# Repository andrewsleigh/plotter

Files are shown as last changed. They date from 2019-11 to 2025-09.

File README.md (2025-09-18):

<p>
<div class="video-responsive">
<iframe width="800" height="450" src="https://www.youtube.com/embed/pfx2bN_xx8s" frameborder="0" allow="accelerometer; autoplay; encrypted-media; gyroscope; picture-in-picture" allowfullscreen></iframe>
</div>
</p>

* **Update: 2020-03-04. I'm currently on version 3 of the design – scroll down to see the current design and download files**
* **Update: 2021-07-06. I've added a [BOM](#bom), after many requests!**
* **Update: 2021-11-25. Added an alternative [US-centric BOM](#us-bom), shared by a fellow maker**
* 

## Support my work!

If you like this project or would like to say thanks, you can buy my plotter artwork from https://penuppendown.square.site. I'd really appreciate your support :) 

## Background

I've always enjoyed the aesthetics of pen plotters, both in the way they operate, and their output. And unlike most digital machines that interface with the physical world, they actually get better at the transition point. Laser cutters make a smell, they burn or melt edges and leave behind a kerf. 3D printers are slow, and leave behind layer lines or heaps of PLA spaghetti. But pen plotters have a delightful slow, deliberate movement that is both cleanly digital and unavoidably textured.

I have an old HP 7475A plotter, but I wanted to try making my own. Not least because I've just made a 1-axis CNC machine ([a camera slider](../fab-slider)) so wanted to continue learning by adding another axis. In particular, I learned from the previous project that getting a machine to 90% good enough is easy. The real work is in that last 10%. If I want to create really good plots, I need to make a really good plotter.

## Version 1: Endless Plotter

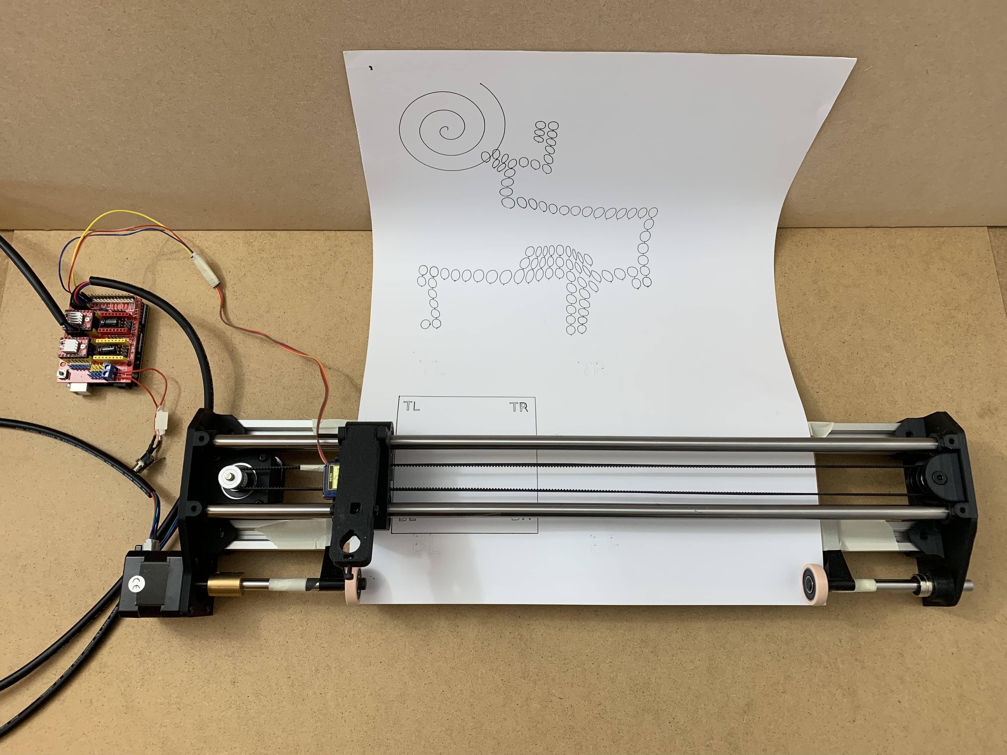
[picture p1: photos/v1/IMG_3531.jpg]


I was inspired to start this project when I saw [this plotter featured on Hackaday](https://hackaday.com/2019/08/26/3d-printed-pen-plotter-is-as-big-as-you-need-it-to-be/). As well as being nicely finished, it has a clever design that moves the pen in one axis, and the paper in the other, much like a commercial plotter or inkjet printer.

This has a couple of nice benefits: 
* It has a more compact footprint (when not in use) – it's only as big as its x-axis.
* It can, in theory, plot an endlessly large (in the y-axis) piece of artwork.

I made a version of this plotter, adapting the original 3D files and had some success  with it in practice, but I eventually decided this format was too compromised for me – I couldn't get the paper to feed back and forth reliably. So I switched to a more traditional 'Cartesian' format for version 2, where the y-axis is carried on top of the x-axis, and the plotter sits on top of the paper.

However, I've shared my 3D files here for others to use if interested. Most of the parts have been redesigned from scratch, except for the pen carriage, which is pretty close to the original design by [Ufficio Progetti Perduti](https://www.thingiverse.com/thing:3789969)

* [3D files on Thingiverse](https://www.thingiverse.com/thing:3986756)
* [3D files on Github](https://github.com/andrewsleigh/plotter/tree/master/3d-parts/v1)
* [Photos on Github](https://github.com/andrewsleigh/plotter/tree/master/photos/v1)

## Version 2: Cartesian Plotter

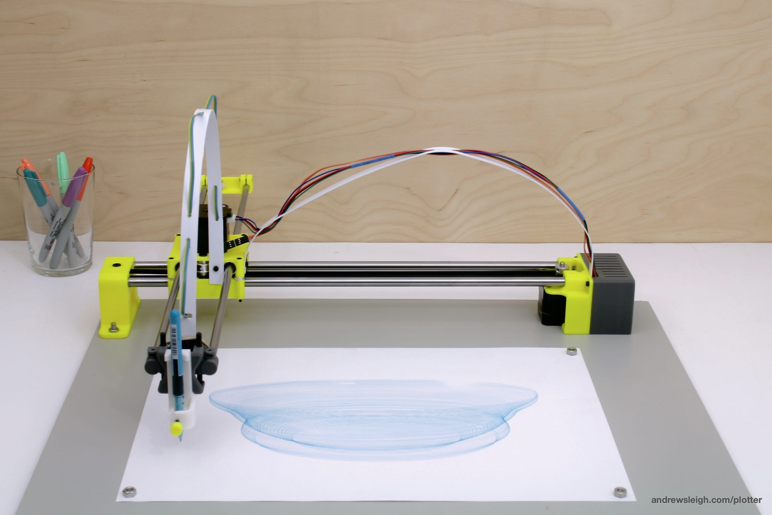
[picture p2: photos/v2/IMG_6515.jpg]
Plotter v2


This version builds on what I learned with version 1. Most obviously, it uses a traditional 'cartesian' design, where movement in the y-axis is provided by a motorized arm, while the drawing surface stays still. This has the benefit of much greater accuracy. It also means that you can, in theory, draw on any flat surface. 

However the drawbacks are that:

1. It needs much more space. With about 50 cm of travel in each axis, it needs a space that big to store, and 1 m x 50 cm to operate.
2. The long arm (with steel rods in my case) is heavy, so it tends to dip towards the end of its reach. This can cause problems getting the right pen height or pressure. To alleviate this, my design has bolt-down points on the x-axis. By bolting this axis to a piece of plywood, the frame is much stiffer. 

Some other features worth noting: 

* I'm using small sections of kite poles to hold the two parts of the pen lifter assembly together. I found 0.1 mm of extra clearance on one part was enough to allow smooth running without wobble.

* In an idea I lifted from Evil Mad Scientist's AxiDraw, I'm using thin strips of flexible polypropylene plastic to support the wires to the servo and y-axis stepper. 

### 3D design

* [3D files on Thingiverse](https://www.thingiverse.com/thing:4037180)
* [3D files on Github](https://github.com/andrewsleigh/plotter/tree/master/3d-parts/v2)
* [Photos on Github](https://github.com/andrewsleigh/plotter/tree/master/photos/v2)

### Photos and video

<p>
<div class="video-responsive">
<iframe width="800" height="450" src="https://www.youtube.com/embed/Z99n9q5OYKk" frameborder="0" allow="accelerometer; autoplay; encrypted-media; gyroscope; picture-in-picture" allowfullscreen></iframe>
</div>
</p>

There's a short demo on YouTube: <https://youtu.be/Z99n9q5OYKk>  
And lots of photos on Github: <https://github.com/andrewsleigh/plotter/tree/master/photos/v2>

## Version 3: Cartesian Plotter with V-slot axis

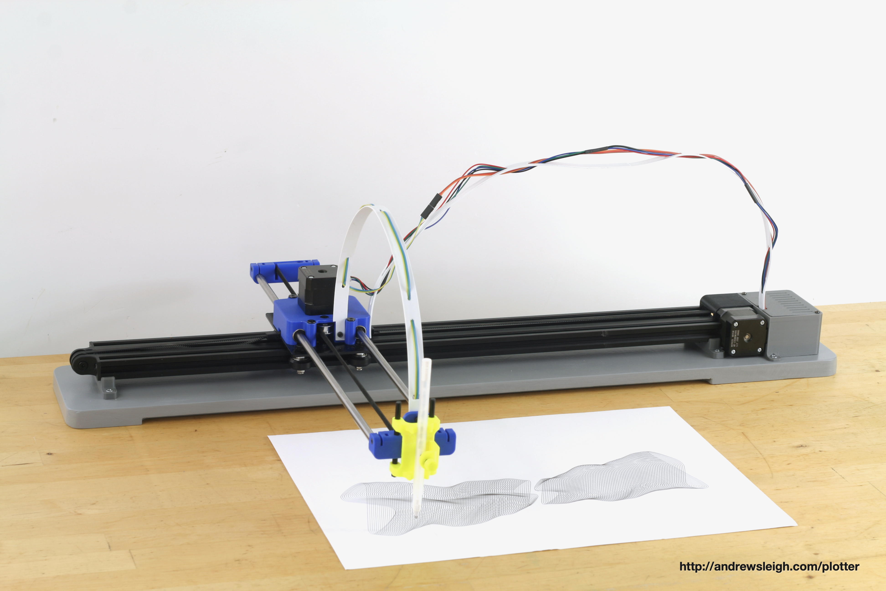
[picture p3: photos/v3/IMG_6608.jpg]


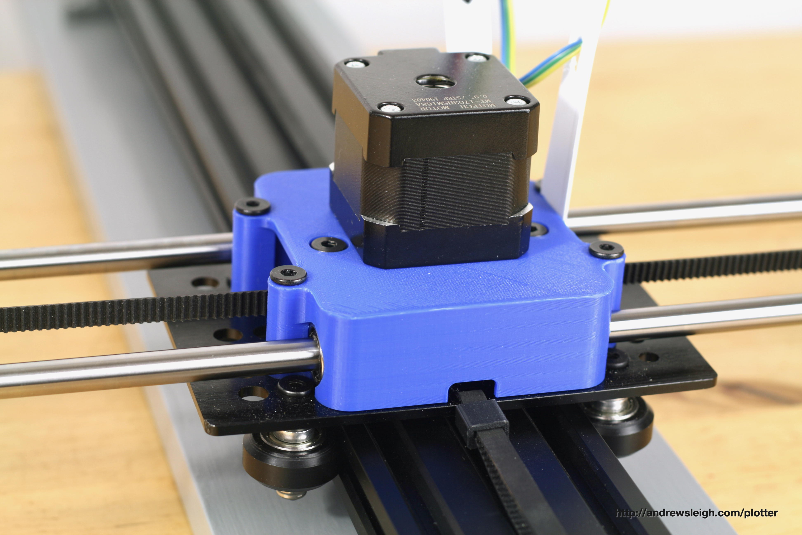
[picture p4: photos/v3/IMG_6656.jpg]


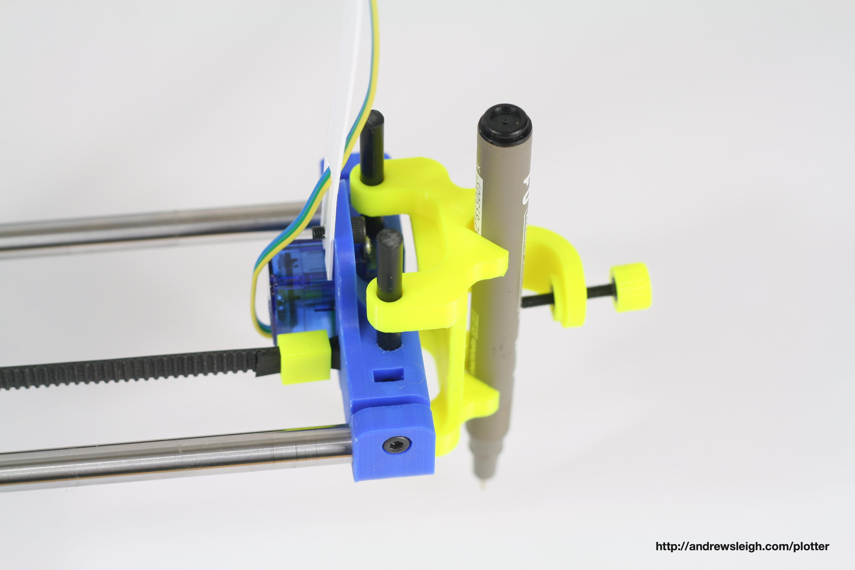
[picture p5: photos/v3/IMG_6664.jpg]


Previous designs used 10mm steel rods for the x-axis. These are prone to flexing in the assembly, and the linear bearings are also noisy. So I wanted to switch to a design that used a wheeled gantry sliding on v-slot aluminium extrusion. 

I tried a quick test by hacking a previous project and bolting my existing y-axis to a single axis slide I already had. This worked very well and convinced me it would be worth building a proper x-axis with v-slot.

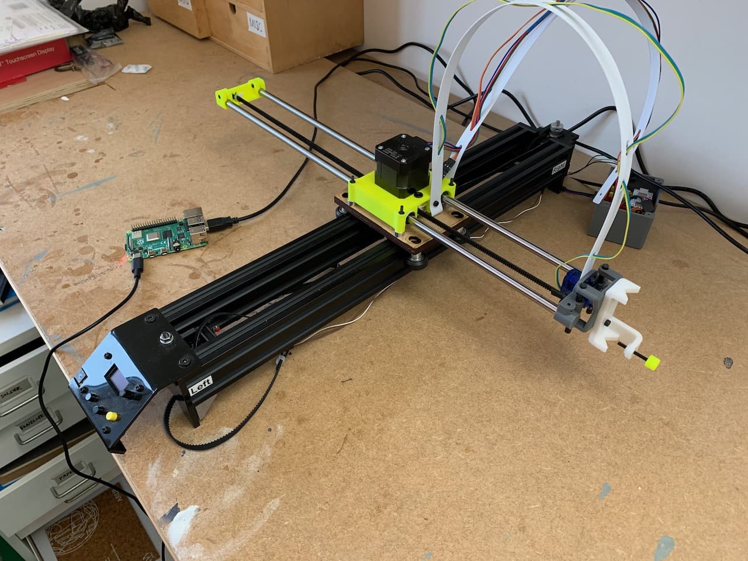
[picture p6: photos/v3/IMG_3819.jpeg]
Plotter v3 prototype


I already had 2 lengths of 2020 v-slot from my first build, so I initially used these, and made a simple assembly that gained rigidity by bolting these down to a wooden base. 

I ordered a standard v-slot gantry from China, which cost about £10-12, including wheels, bolts and spacers – including eccentric spacers. This allowed me to get a very good fit of the gantry on the x-axis for smooth quiet motion. 

If you don't want to buy an aluminum gantry, could can easily cut one on a laser (as I did for my prototype) or 3D print one from the OpenBuilds design. 

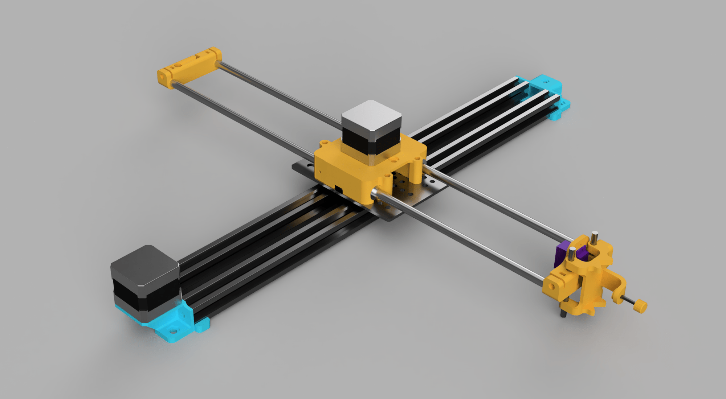
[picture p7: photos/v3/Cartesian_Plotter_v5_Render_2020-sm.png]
Plotter v3 2020


Note, you'll need to tap M5 holes into the ends of the v-slot to attach the two end brackets. The feet are bolted from underneath into the v-slot. 

But then I came into the possession(!) of a 70 cm lngth of 2060 v-slot, so I was able to make a longer, even more stable x-axis. I needed to switch the orientation of the x-axis motor, and raise the axis a little more off the ground to enable th timing belt to go over and under the 2060. I also had to fit a larger 30 tooth pulley. 

But otherwise the principle is the same, I just did a little more work to integrate the electronics and motor. 

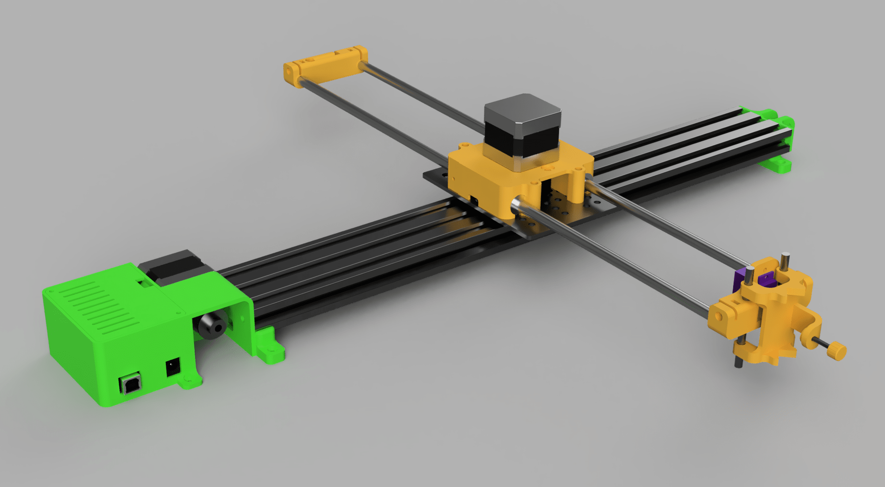
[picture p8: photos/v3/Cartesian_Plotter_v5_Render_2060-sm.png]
Plotter v3 2060


### 3D design

* [3D files on Thingiverse](https://www.thingiverse.com/thing:4200863)
* [3D files on Github](https://github.com/andrewsleigh/plotter/tree/master/3d-parts/v3)
* [3D assembly on Fusion online](https://a360.co/48olCzT)
* [Photos on Github](https://github.com/andrewsleigh/plotter/tree/master/photos/v3)

### Improvements over earlier versions

* More stable x-axis (and so less drooping of the pen at it's furthest y-extension)
* Much quieter motion on the x-axis, after swapping out linear bearings fora wheeled gantry
* X-axis can be screwed down to a solid base for greater stability
* Improved brackets for timing belt and linear rods on y-axis so belt can be more easily removed or tightened
* Simplified and more compact pen lifter
* Housing for Arduino and CNC shield can be removed or re-modelled easily (e.g. to fit a smaller Nano-based CNC shield)
* Base has a rebate to fit a 60 cm cutting mat, to allow easier alignment of paper for plotting

<a name="bom"/>

## Bill of Materials (BOM)

It’s difficult to give a comprehensive BOM because there is so much flexibility in the design, and so many choices depend on what you have to had. Nevertheless, here is an attempt at a reasonable baseline.

### Motion Control

* Arduino Uno (I’d recommend a genuine Arduino to reduce the risk of EM interference which can play havoc with your servo motor)
* Motor Control Shield
* 2 x Stepper Drivers (A4988-style, but I’d recommend Trinamic drivers for quieter operation)
* 2 x Nema 17 Stepper motors (‘17’ refers to the physical size, you will need to specify the power as well. I used these 7 oz ones from Ooznest, which are fine: https://ooznest.co.uk/product/nema17-stepper-motors/

I’m this configuration the motor control shield is mounted on the Arduino, and the stepper drivers mounted on the shield. You can also get versions that mount a smaller Arduino Nano on to the shield, alongside the drivers, which would make for a more compact design that does the same thing. You would need to adapt the Arduino housing to fit this config.

### X Axis

* Length of 2060 V-Slot aluminium extrusion.
 
(I used a 75 cm length, but anything from 40 cm up is good. Make sure you use V slot and not one of the other profiles of extrusion.An earlier version used two lengths of 2020 extrusion with a 20 mm gap in between. It doesn’t matter, just use what you have. A single piece of 2060 is stiffer, which means less drooping of the pen end and so more reliable plotting, but you could easily make other designs stiffer.)

You will need to tap M5 holes in the ends of the extrusion. 

* 2GT Timing belt (buy a length about 2.5 x the length of your extrusion. (e.g. https://ooznest.co.uk/product/2gt-gates-open-timing-belt-per-metre/)

* 30-tooth 2GT pulley (for 6 mm belt, 5 mm bore) e.g. https://ooznest.co.uk/product/2gt-pulleys/

(This pulley has a large enough diameter to run the belt on either side of the extrusion. If you want to run the belt in a gap inside some extrusion (or you’re using the 2020 design) you’ll need a smaller diameter pulley. You could print one.)

* Idler pulley (of roughly the same diameter as your main pulley) e.g. https://ooznest.co.uk/product/2gt-smooth-idler/. You could also print one.

3D printed parts:

* End bracket for idler pulley
* End bracket for motor
* Shield for motor end (purely cosmetic)
* Box and lid for Arduino
* Feet

### Gantry and Y-axis

* Large v-slot gantry kit (I got mine direct from China, or you can laser cut or 3D print your own)
* 2 x small idler pulleys for y-axis (not the larger Openbuilds pulleys)
* 4 x 8 mm (8UU) linear bearings 
* 2 x 8 mm linear rods

3D printed parts:

* Gantry case

### Pen Lifter

* SG90 Servo motor (e.g. https://thepihut.com/products/towerpro-servo-motor-sg90-hv-continuous-rotation)
* 3 wire jumper extension to extend the wires form the servo back to the motor control board
* 2 x smooth 5 mm diameter rods (I used rods from an old kite. Any smooth, consistent-diameter rods will do, but you will need to adapt the 3D files to fit)

3D printed parts:

* Y axis pen end bracket
* Y axis other end bracket
* Pen lifter
* 3mm bolt cap

### Other Hardware

* Low profile M5 bolts to attach brackets to V-Slot
* Various M3 bolts and nutes (get a selection box)
* Drop-in Tee Nuts for V-Slot e.g. https://ooznest.co.uk/product/drop-in-tee-nuts/
* Some GT2 belt clips, such as cable ties, or these nice removable clips: <http://www.thingiverse.com/thing:2354961>

(In the UK, I'd recommend Ooznest for all the materials you need to buy.)

<a name="us-bom"/>

## BOM (USA)

Fellow plotter plotter ('plotterer'?) [Kameron Keller](https://www.kameronkeller.com) kindly shared this BOM that he put together based on his build. And he's based in the US, so there are some US Amazon links in there which may be useful to some. Thanks Kameron.

| Part Number | Qty | Description | PRICE EA. | Description | Link |
| --- | --- | --- | --- | --- | --- |
| M5 - .80 | 2 | LOCKING NUT | 0.4 | FOR IDLER PULLEYS | |
| M3 X 8 | 4 | SCREW | 0.27 | WIRE GUIDE- FOR MOUNTING PLASTIC ON Y-AXIS (2)<br>(2) FOR HOLDING ARDUINO TO BOX | |
| M5 X 10 | 3 | SCREW - COUNTERSUNK | 0.35 | USED 2 FOR LARGE IDLER PULLEY 3D PRINTER PART MOUNTING TO 2060 RAIL | |
| M3 X 6 | 17  | SCREW | 0.23 | USED 12<br>X-AXIS WIRE HOLDER (2)<br>NEMA 17 MOUNTING (8)<br>ARDUINO LID (2) | |
| M3 X 12 | 4 | SCREW - PAN HEAD | 0.33 | LINEAR ROD CLAMP SCREWS (4) | |
| M3 - .5 | 14  | NUT | 0.13 | USED 12<br>LINEAR ROD CLAMP (4)<br>WIRE GUIDE (4)<br>X-AXIS WIRE HOLDER (2)<br>MOUNTING ARDUINO TO BOX (2) | |
| M3 X 30 | 1 | SCREW - SOCKET HEAD | 0.85 | PEN HOLDER | |
| M5 | 10  | WASHERS | 0.14 | USED 8 FOR IDLER PULLEY | |
| M5 X 10 | 4 | SCREW - PAN HEAD | 0.35 | 2060 VSLOT BASES | |
| M5 X 8 | 2 | SCREW - PAN HEAD | 0.2 | USED 2 FOR MOUNTING STEPPER MOTOR TO 2060 RAIL (ON END WITH ARDUINO) | |
| M5 X 35 | 4 | SCREW - PAN HEAD | 0.55 | FOR MOUNTING STEPPER MOTOR ASSEMBLY TO GANTRY PLATE, HAD TO CUT DOWN FOR CLEARANCE | |
| M5 - .80 | 8 | NUT | 0.16 | STEPPER MOTOR ASSEMBLY TO GANTRY PLATE (4) | |
| M5 X 25 | 3 | SCREW - COUNTERSUNK | 0.55 | USED 2 FOR IDLER PULLEYS | |
| SG-90 | 1 | SERVO | 2.75 | PIN LIFTER (4 PACK, $10.99) | [https://www.amazon.com/gp/product/B07MLR1498/ref=ppx\_yo\_dt\_b\_asin\_title\_o05\_s03?ie=UTF8&psc=1](https://www.amazon.com/gp/product/B07MLR1498/ref=ppx_yo_dt_b_asin_title_o05_s03?ie=UTF8&psc=1) |
| | 2 | 7 CM X 5MM CARBON RODS | 12.49 | PEN LIFTER (FOR 5 PCS, CUT DOWN TO 7 CM) | [https://www.amazon.com/gp/product/B07P81VMPF/ref=ppx\_yo\_dt\_b\_asin\_title\_o04\_s00?ie=UTF8&psc=1](https://www.amazon.com/gp/product/B07P81VMPF/ref=ppx_yo_dt_b_asin_title_o04_s00?ie=UTF8&psc=1) |
| | 2 | LINEAR RODS 8MM X 500MM | 9.95 | Y AXIS (2 PACK) | [https://www.amazon.com/gp/product/B07DPFH7HL/ref=ppx\_yo\_dt\_b\_asin\_title\_o05\_s02?ie=UTF8&psc=1](https://www.amazon.com/gp/product/B07DPFH7HL/ref=ppx_yo_dt_b_asin_title_o05_s02?ie=UTF8&psc=1) |
| | 66  | GT2 TIMING BELT ~ 66 INCHES | 11.99 | CAME WITH 196 INCHES | [https://www.amazon.com/gp/product/B0776KXY8G/ref=ppx\_yo\_dt\_b\_asin\_title\_o05\_s01?ie=UTF8&psc=1](https://www.amazon.com/gp/product/B0776KXY8G/ref=ppx_yo_dt_b_asin_title_o05_s01?ie=UTF8&psc=1) |
| | 1 | 20 TOOTH, 5MM TIMING PULLEY ^ INCLUDED WITH BELT | | CAME IN 8 PACK | |
| | 4 | LINEAR BEARINGS, 8 X 15 X 24MM | 0.84 | CAME IN 12 PACK | [https://www.amazon.com/gp/product/B08GSK5ZQB/ref=ppx\_yo\_dt\_b\_asin\_title\_o05\_s03?ie=UTF8&psc=1](https://www.amazon.com/gp/product/B08GSK5ZQB/ref=ppx_yo_dt_b_asin_title_o05_s03?ie=UTF8&psc=1) |
| | 2 | 5MM IDLER PULLEYS FOR 6MM TIMING BELT<br>INNER DIAMETER = 12 MM<br>FLANGE DIAMETER = 18 MM<br>BORE = 5MM<br>WIDTH = ~9MM | 1.6 | (CAME IN PACK OF 5) | [https://www.amazon.com/gp/product/B01H3F8LUU/ref=ppx\_od\_dt\_b\_asin\_title\_s03?ie=UTF8&psc=1](https://www.amazon.com/gp/product/B01H3F8LUU/ref=ppx_od_dt_b_asin_title_s03?ie=UTF8&psc=1) |
| | 1 | GANTRY PLATE KIT | 39.59 | | [https://www.amazon.com/gp/product/B08LDM3QFD/ref=ppx\_yo\_dt\_b\_asin\_title\_o05\_s01?ie=UTF8&psc=1](https://www.amazon.com/gp/product/B08LDM3QFD/ref=ppx_yo_dt_b_asin_title_o05_s01?ie=UTF8&psc=1) |
| | 1 | 2060 LINEAR RAIL - 500MM | 21.99 | | [https://www.amazon.com/gp/product/B08GCQXDBR/ref=ppx\_yo\_dt\_b\_asin\_title\_o05\_s00?ie=UTF8&psc=1](https://www.amazon.com/gp/product/B08GCQXDBR/ref=ppx_yo_dt_b_asin_title_o05_s00?ie=UTF8&psc=1) |
| | 2 | NEMA 17 42MM X 40MM, 0.46 NM TORQUE | 17.59 | | [https://www.amazon.com/gp/product/B06XSYP24P/ref=ppx\_yo\_dt\_b\_asin\_title\_o05\_s01?ie=UTF8&psc=1](https://www.amazon.com/gp/product/B06XSYP24P/ref=ppx_yo_dt_b_asin_title_o05_s01?ie=UTF8&psc=1) |
| | 6 | SMALL WOOD SCREWS FOR MOUNTING ENTIRE ASSEMBLY TO PIECE OF WOOD | | | |
| | 2 | SMALL SCREWS FOR MOUNTING ARDUINO LID | | | |
| | 4 | M5 T-SLOT NUTS | 0.08 | | [https://www.amazon.com/gp/product/B07NZKK1PM/ref=ppx\_yo\_dt\_b\_asin\_title\_o02\_s00?ie=UTF8&psc=1](https://www.amazon.com/gp/product/B07NZKK1PM/ref=ppx_yo_dt_b_asin_title_o02_s00?ie=UTF8&psc=1) |
| | 1 | ARDUINO UNO CNC KIT (off brand) | 17.99 | | [https://www.amazon.com/gp/product/B06XHKSVTG/ref=ppx\_yo\_dt\_b\_asin\_title\_o05\_s03?ie=UTF8&psc=1](https://www.amazon.com/gp/product/B06XHKSVTG/ref=ppx_yo_dt_b_asin_title_o05_s03?ie=UTF8&psc=1) |
| | 1 | CNC SHIELD EXPANSION BOARD | | CAME WITH ARDUINO KIT | |
| | 2 | A4988 DRIVERS | | CAME WITH ARDUINO KIT - JUMPERS INCLUDED | |
| | 1 | 30 TOOTH 5MM BORE TIMING PULLEY | 3.99 | CAME IN PACK OF 2 | [https://www.amazon.com/gp/product/B089LW6XTV/ref=ppx\_yo\_dt\_b\_asin\_title\_o05\_s03?ie=UTF8&psc=1](https://www.amazon.com/gp/product/B089LW6XTV/ref=ppx_yo_dt_b_asin_title_o05_s03?ie=UTF8&psc=1) |
| | 1 | PLASTIC FOR SALE SIGN USED FOR MAKING WIRE HOLDERS | 4.99 | | |
| | 1 | SMOOTH IDLER PULLEY KIT | 5.99 | | [https://openbuildspartstore.com/smooth-idler-pulley-kit/](https://openbuildspartstore.com/smooth-idler-pulley-kit/) |

## Electronics

I'm using an Arduino Uno with a CNC shield and two stepper drivers. I prototyped with the standard (and cheap) A4988 drivers, but switched over to Trinamic drivers which chop much more smoothly down to 1/256 microsteps, resulting in much quieter motion.

You can use pretty much any Trinamic driver board. There is a good comparison here: <https://learn.watterott.com/silentstepstick/comparison/>

## Power

The plotter requires 12V power, and your supply should be good enough to supply the current your steppers demand. (Mine is a 1.5A 12V supply)

You can plug this straight into the 12V barrel jack on the Arduino, which will give 5V reulated power to the Arduino, and 12V onto the CNC shield. 

**BUT YOU MUST HACK YOUR CNC SHIELD FIRST:** You need to wire the VIN pin on the CNC shield to the positive power terminal. Like this: http://3dpburner.blogspot.com/p/bluetooth-connection.html?m=1

### Software and Workflow

The plotter expects G-Code commands. Typically these are used by CNC machines such as mills, 3D printers and laser cutters. Most of the instructions are shared between machine types except at the business end. The plotter expects pen up and pen down commands to move the pen. (In HPGL, the language used by HP plotters, these are `PU` and `PD`.) Here, we can piggy back on G-Code commands intended to control the power of a laser. So where a laser cutter might start a line by switching the laser on to a certain power, we can use the same command but send it to the servo to move the wiper and drop the pen. This is what the modified Grbl firmware does. 

The chain of tools/processes is basically:

Create artwork > export as vectors (SVG, PDF, etc) > Create GCODE from vector file > Stream GCODE to Arduino > Use Grbl firmware on Arduino to control motors

### Art

Most of my plots are procedurally generated in Processing or p5. I write sketches that are optimised to create continuous lines and curves: no pixel data or, colours or line styles. So far, I haven't figured out a way to use the 3D renderer in p5, and still be able to export the artwork as an SVG. Either way, I start with vector line art.

I also use Blender, which has loads of options for exporting 2D vector data from 3D models.

### Create GCODE

After too much time wasted with Inkscape plug-ins I have switched to [Lightburn](https://lightburnsoftware.com) to create GCode. I find it works well with PDF files.

### Stream GCODE

There are numerous GRBL interfaces available, and I've always had good results with [CNCJS](https://cnc.js.org), which is bundled up as a webview inside a Mac app. However, that can hog the machine CPU, and also means your laptop is tethered to the plotter. So now I [run CNCJS on a local Node server on a Raspberry Pi](https://cnc.js.org/docs/rpi-setup-guide/) (Model 4, 2GBRAM) connected by USB cable to the plotter. It auto-runs as soon as the Pi boots, and I can access it through a web browser to start a job or check in later. I can always switch to CNCJS running on the laptop by unplugging the Pi.

The plotter expects a stream of GCode commands to control the motors. There are many ways you can chain together software to get to this stage. Working backwards from the plotter:

### Motor control

The Arduino is loaded with Grbl firmware, pretty much stock, but I'm using one of the many variants that lets you control a servo for pen up and pen down.

<https://github.com/robottini/grbl-servo>

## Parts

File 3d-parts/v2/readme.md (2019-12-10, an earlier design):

# Readme

These parts are for version 2 of the plotter, which uses a cartesian design.

These are STL exports from Fusion 360. There is also a Fusion 360 archive file of the whole model.

If you'd like to remix this model, please take a look at the [Thingiverse project page](https://www.thingiverse.com/thing:4037180) and consider adding attribution there.

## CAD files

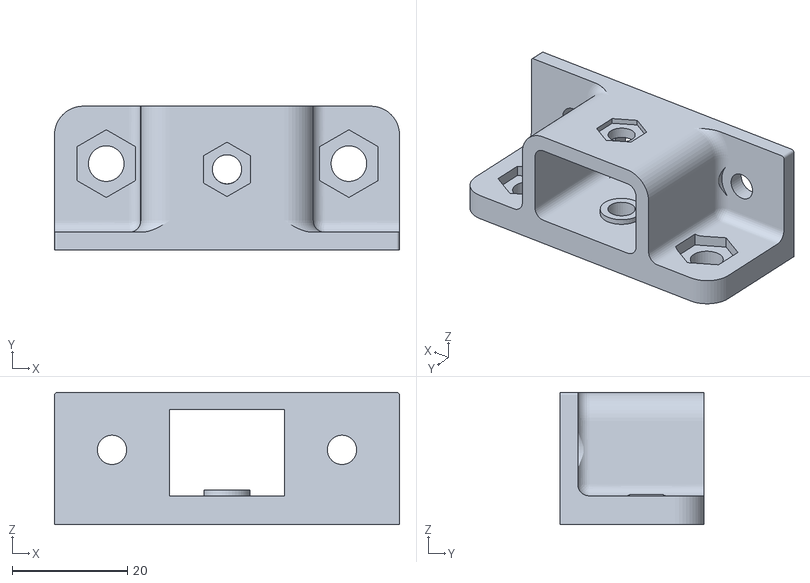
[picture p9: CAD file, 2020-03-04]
3d-parts/v3/2020_x-axis/2020_x-axis_other-end-bracket.stl
60.0 x 25.0 x 23.0

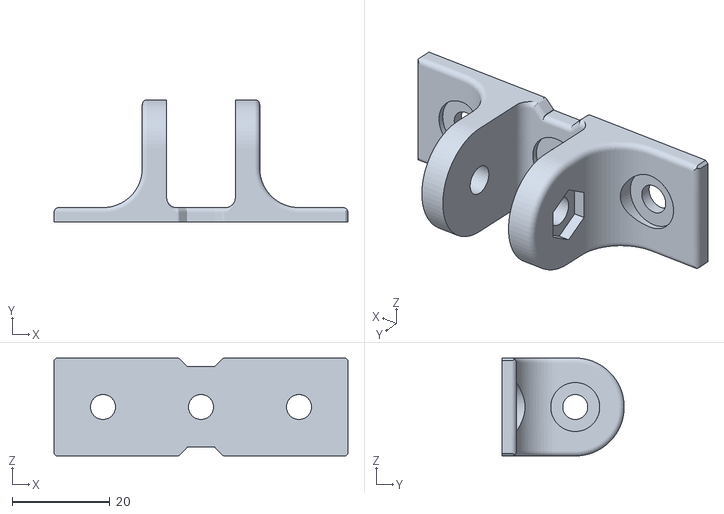
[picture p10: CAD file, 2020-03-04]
3d-parts/v3/2060_x-axis/2060_x-axis_other-end-bracket.stl
60.0 x 25.0 x 20.0

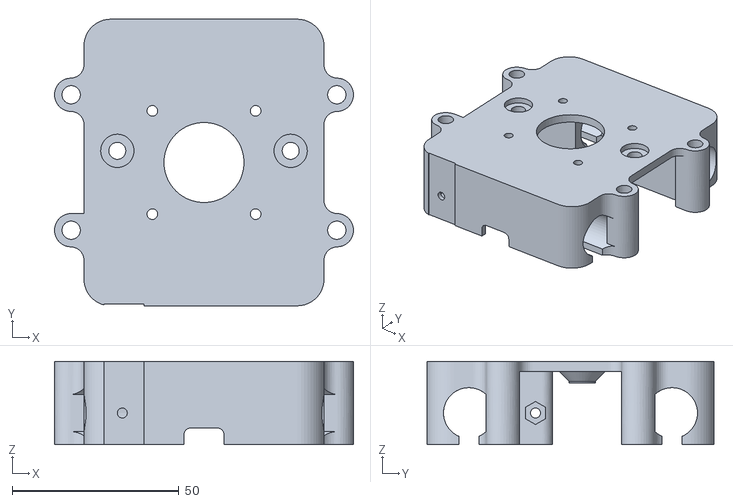
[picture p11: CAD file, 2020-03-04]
3d-parts/v3/y-axis/y-axis_gantry.stl
89.7 x 86.0 x 25.0

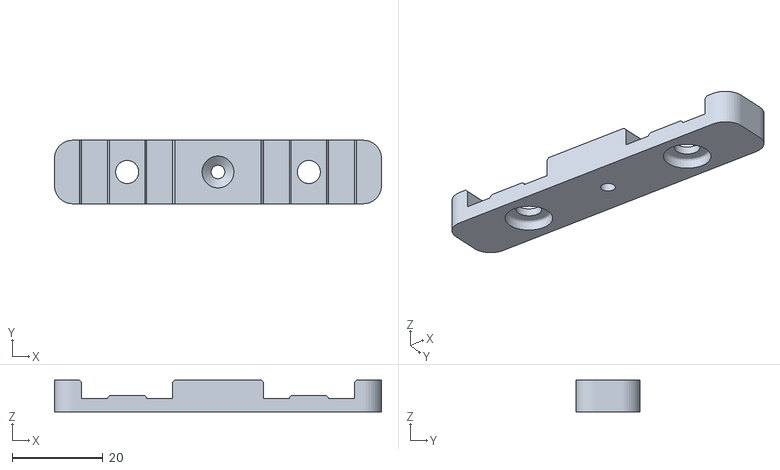
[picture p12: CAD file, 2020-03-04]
3d-parts/v3/2020_x-axis/2020_x-axis_foot.stl
72.0 x 14.0 x 7.00

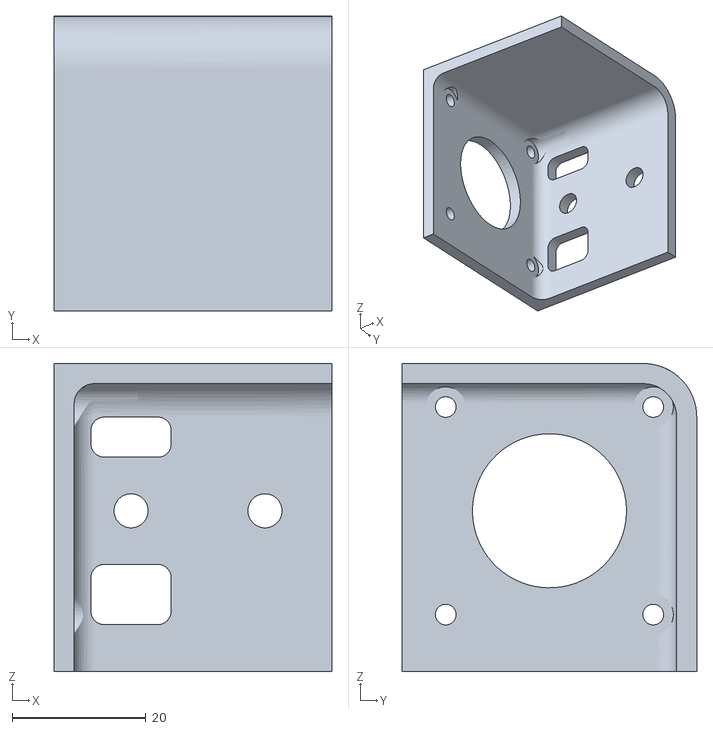
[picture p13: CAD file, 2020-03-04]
3d-parts/v3/2060_x-axis/2060_x-axis_motor-end-bracket.stl
41.5 x 44.0 x 46.0

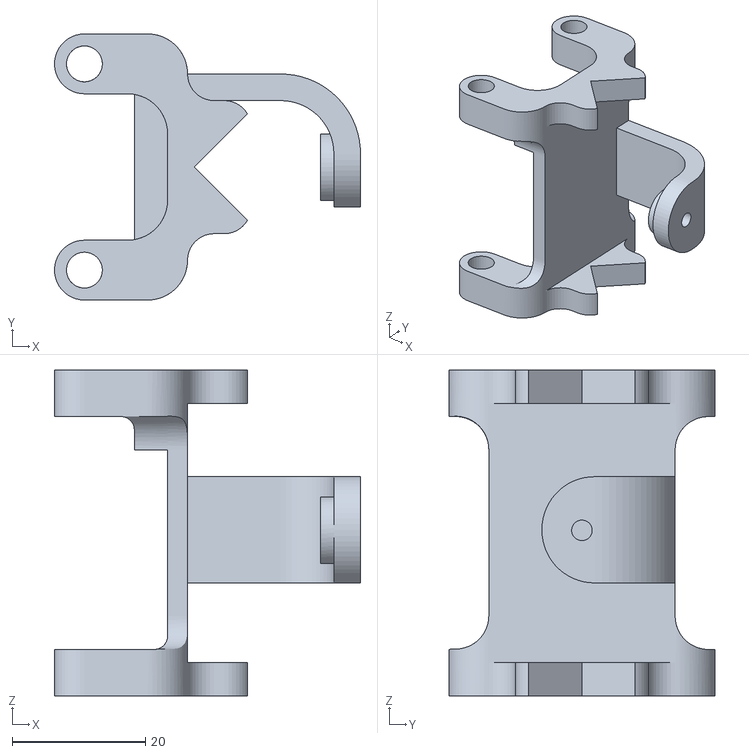
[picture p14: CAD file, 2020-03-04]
3d-parts/v3/y-axis/y-axis_pen-lifter.stl
46.0 x 40.0 x 49.0

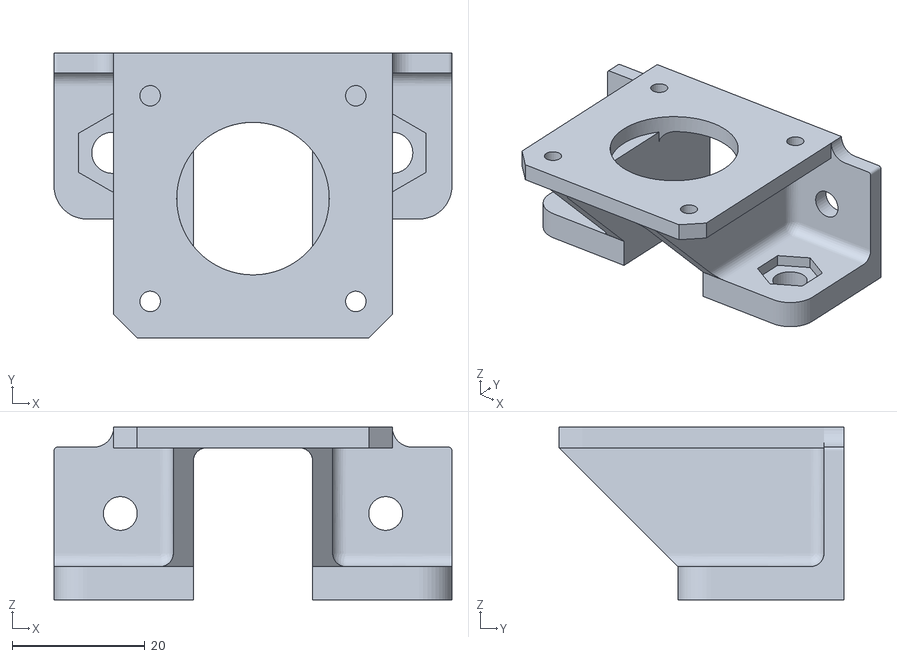
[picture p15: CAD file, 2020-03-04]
3d-parts/v3/2020_x-axis/2020_x-axis_motor-end-bracket.stl
60.0 x 42.9 x 26.0

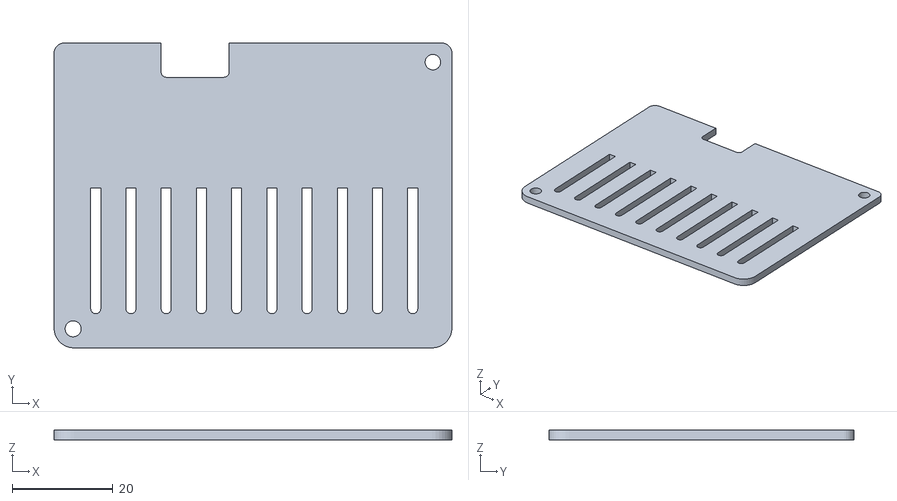
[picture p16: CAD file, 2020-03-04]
3d-parts/v3/2060_x-axis/2060_arduino-box-lid.stl
79.1 x 60.6 x 2.00

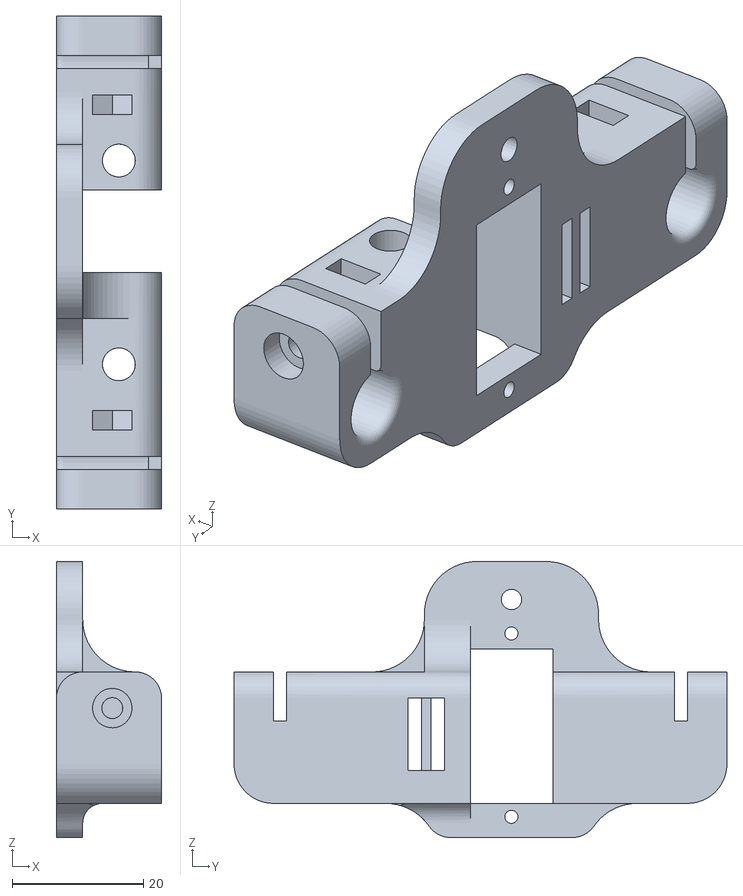
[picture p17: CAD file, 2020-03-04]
3d-parts/v3/y-axis/y-axis_pen-end.stl
16.0 x 75.0 x 42.0

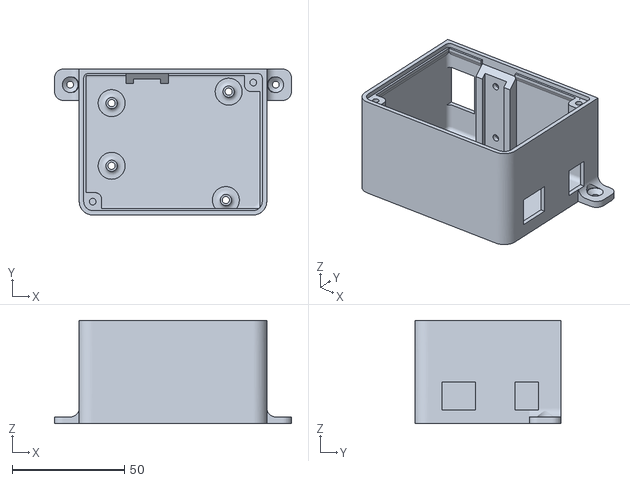
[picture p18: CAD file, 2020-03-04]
3d-parts/v3/2060_x-axis/2060_arduino-box.stl
105.5 x 65.0 x 46.0

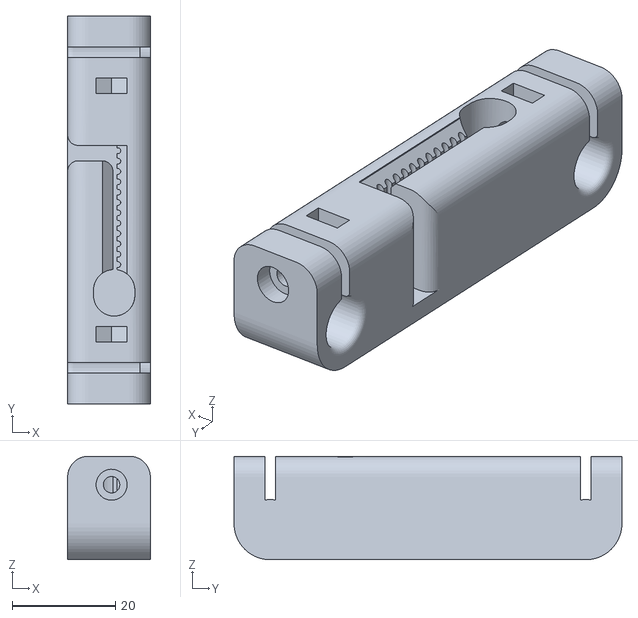
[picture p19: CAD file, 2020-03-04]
3d-parts/v3/y-axis/y-axis_other-end.stl
16.0 x 75.0 x 20.0

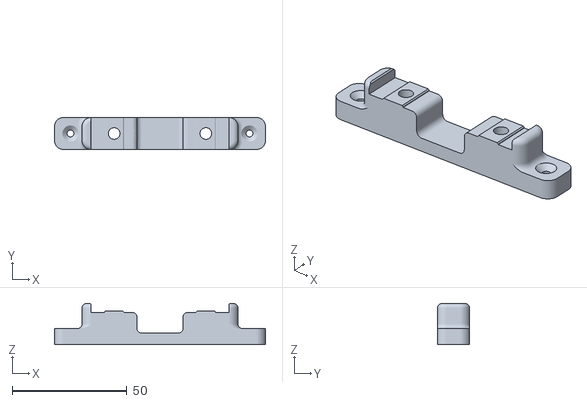
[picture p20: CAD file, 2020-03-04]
3d-parts/v3/2060_x-axis/2060_x-axis_foot.stl
92.0 x 14.0 x 18.0

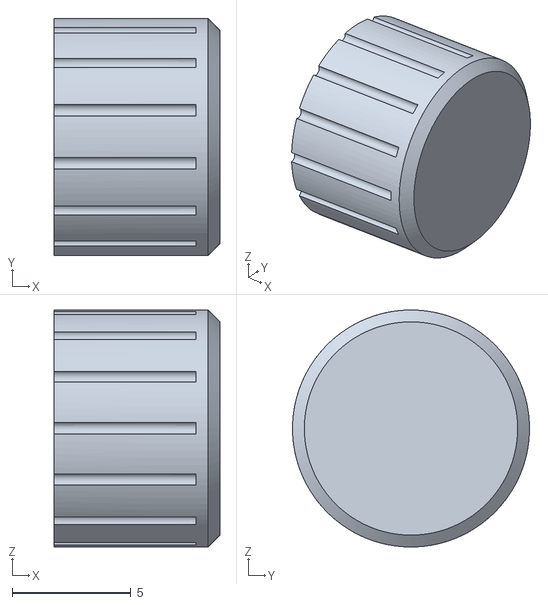
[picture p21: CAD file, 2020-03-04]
3d-parts/v3/y-axis/m3_screw_cap.stl
7.00 x 10.0 x 10.0

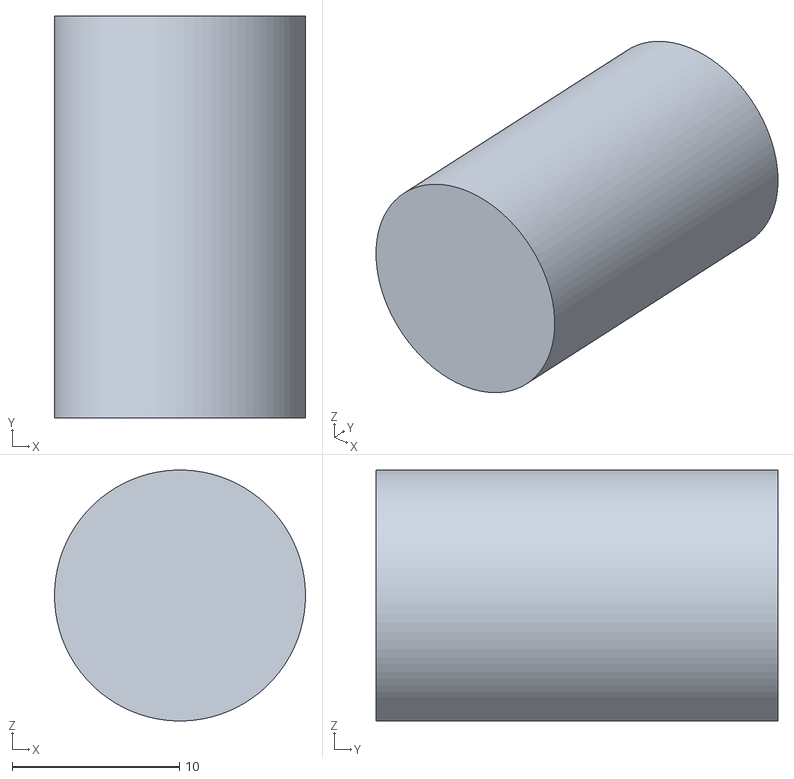
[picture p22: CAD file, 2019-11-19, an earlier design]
3d-parts/v1/Linear bearing 8UU.stl
15.0 x 24.0 x 15.0

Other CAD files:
3d-parts/v2/X axis other end.stl
3d-parts/v1/V-Slot 2020x500.stl
3d-parts/v2/Pen grip - lower.stl
3d-parts/v1/Linear Rod 10x500.stl
3d-parts/v1/End Cap - Motor.stl
3d-parts/v1/End Cap - Opposite.stl
3d-parts/v1/Idler pulley.stl
3d-parts/v1/Linear Rod 8x500.stl
3d-parts/v1/Linear bearing LM10UU.stl
3d-parts/v1/Pen carriage lower.stl
3d-parts/v1/Pen carriage top.stl
3d-parts/v1/Servo.stl
3d-parts/v1/Skate Bearing Tyre.stl
3d-parts/v1/Skate Roller Mount.stl
3d-parts/v1/Skate bearing.stl
3d-parts/v2/Arduino case.stl
3d-parts/v2/Bottom gantry.stl
3d-parts/v2/Top gantry.stl
3d-parts/v2/X axis motor end.stl
3d-parts/v2/Y axis cap.stl
3d-parts/v2/Y axis lifter.stl
3d-parts/v2/Y axis other end.stl

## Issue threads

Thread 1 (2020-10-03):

More information for the parts

TheNoim, 2020-10-03:
Hi,

Currently, I try to recreate your project for a student project. However, I really have problems finding the correct parts. In your readme, you only gave limited information about each part which is a problem. If you try to get the parts on sites like aliexpress, then there are often too many options. For example:

> 30 or 40 tooth pulley for x-axis timing belt

[Kee Pang 1PC GT2 Timing Pulley](https://de.aliexpress.com/item/32900943510.html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,searchweb201602_,searchweb201603_ )

There too many possibilities. And I can not really wait until it arrives, because it just takes to long. The first order needs to be correct. Can you add a list of links? Even though if I don't buy there, at least I would have a complete spec list of each part with images.

I hope you can help me. The project itself seems awesome.

dunklesToast, 2020-10-15:
I've got the same problem :/

andrewsleigh, 2020-10-16:
Hi - it's difficult to make a comprehensive parts list, partly cos I have no free time at the moment, (so maybe something crowd-sourced could help), but also because there is so much freedom in how each person chooses to make it.

That being said, if you look these things up on Ooznest, which is a great UK supplier, they have a small range of the right stuff, and its easy to get a definitive component - you can always look elsewhere to find the equivalent.

Closed 2020-11-16.

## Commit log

2019-11-19 add v1 3d parts
    [End Cap - Motor.stl, End Cap - Opposite.stl, Idler pulley.stl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]
2019-12-10 add v2 3d files
    [Arduino case.stl, Bottom gantry.stl, Pen grip - lower.stl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]
2020-03-04 v3 3d files
    [2020_x-axis_foot.stl, 2020_x-axis_motor-end-bracket.stl, 2020_x-axis_other-end-bracket.stl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]
2020-03-04 rename 3d assemblies
2021-07-06 Add BOM
